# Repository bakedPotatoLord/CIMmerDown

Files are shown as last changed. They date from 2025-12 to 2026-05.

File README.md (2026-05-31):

# CIMmer Down
A project to control 2 drive 2 rev robotics spark ESCs from an arduino nano. 

Coming out of a desire to make use of obsolete parts used by FIRST robotics teams worldwide, we designed a low-cost open source electric longboard. Designed to be accessible to high-school and college students to build, using mostly 3d printed and COTS parts, this project aims to provide an interesting and fun entry into the world of RF electronics, motor control, urethane molding, and more. 

Documentation/Development are not yet complete. Help is always appreciated.

## Features
- Handheld remote
- Status LED
- 2 speed modes
- 16mph top speed
- People of the oposite sex may find you more attractive.
- Disconnection detection and e-stop safety.

## More Details

further, yet incomplete documentation can be found at these pages:

- [Electronics](/Electronics.md)
- [Manufacturing](/Manufacturing.md)

## Selected Media

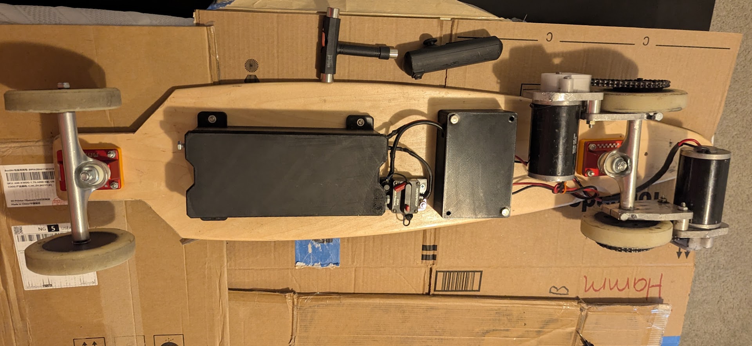
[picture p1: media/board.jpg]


## Why is is called that?
the `CIM` from CIMmer down is a reference to FRC [CIM](https://andymark.com/products/2-5-in-cim-motor) motor.

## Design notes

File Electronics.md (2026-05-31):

# Electronics

These electronics were developed organicaly, and evolved from a wired version of the board.
Along the prototyping process, I switched from an arduino Nano as the longboard controller to an arduino Pro mini 3.3v for both systems.
To be fully honest, this happened because I fried all my arduino nanos, and didn't want to wait for more to ship.

## Schematic

You can download a PDF version of the schematic [here](./media/CimmerDown_schematic.pdf).
when the final revision is complete, I'll put a PNG here.

## Construction

Physically constructing the boards will require some [perfboard](https://en.wikipedia.org/wiki/Perfboard), all the components, and some soldering.

Here is a list of the electrical components to assemble before beginning on making the boards:

### Remote

| Component | Symbol | Quantity | Description |
| --- | --- | --- | --- |
| 10k ohm resistor | R[1-5] | 3 | standard through-hole |
| 100k ohm resistor | R[6-7] | 1 | standard through-hole  |
| 3k3 ohm resistor | R[8] | 1 | standard through-hole |
| status LED | D1 | 1 | standard through-hole; color of your choice! |
| Battery | BT4 | 1 | standard 1S 18650 Li-Ion |
| Arduino Pro Mini  | MOD[1-2] | 1 | 3.3v 8Mhz |
| NRF24L01+ | MOD[3-4] | 1 | standard |
| Analog Joystick | MOD7 | 1 | standard |

### Board

### total
| Component | Symbol | Quantity | Description |
| --- | --- | --- | --- |
| 10k ohm resistor | R[1-5] | 5 | standard through-hole |
| 100k ohm resistor | R[6-7] | 2 | standard through-hole  |
| 3k ohm resistor | R[8] | 1 | standard through-hole |
| 20k ohm resistor | R[9] | 1 | standard through-hole |
| status LED | D1 | 1 | standard through-hole; color of your choice! |
| Battery | BT[1-3] | 3 | CNHL 5.9Ah 3S LiPo |
| Battery | BT4 | 1 | standard 1S 18650 Li-Ion |
| CIM Motor | M[1-2] | 2 | standard |
| Arduino Pro Mini  | MOD[1-2] | 2 | 3.3v 8Mhz |
| NRF24L01+ | MOD[3-4] | 2 | standard |
| REV Robotics Spark ESC | MOD[5-6] | 2 | Obsolete and out of production |
| Analog Joystick | MOD7 | 2 | standard |
| Buck convertor | MOD8 | 1 | 12v to 5v |

Some other consumables include solid core wire, solder, and flux if you prefer.

The perfboard will need to be cut or snapped down to size. The remote requires 23x7 smd holes. The board controller requires __ x __ smd holes.

The following link has an image-based guide showing one way to wire up the boards. it is not difinitively, the only way. if you think you know how to do it better, submit a PR or message me.

[Guide](https://photos.app.goo.gl/4bUh6QA9aAVv1GDRA)

## PCB

A PCB version of the boards might be on the way soon, but I don't know if there's enough interest to warrant it. Lmk if you want one, and what you'd be willing to pay for it.

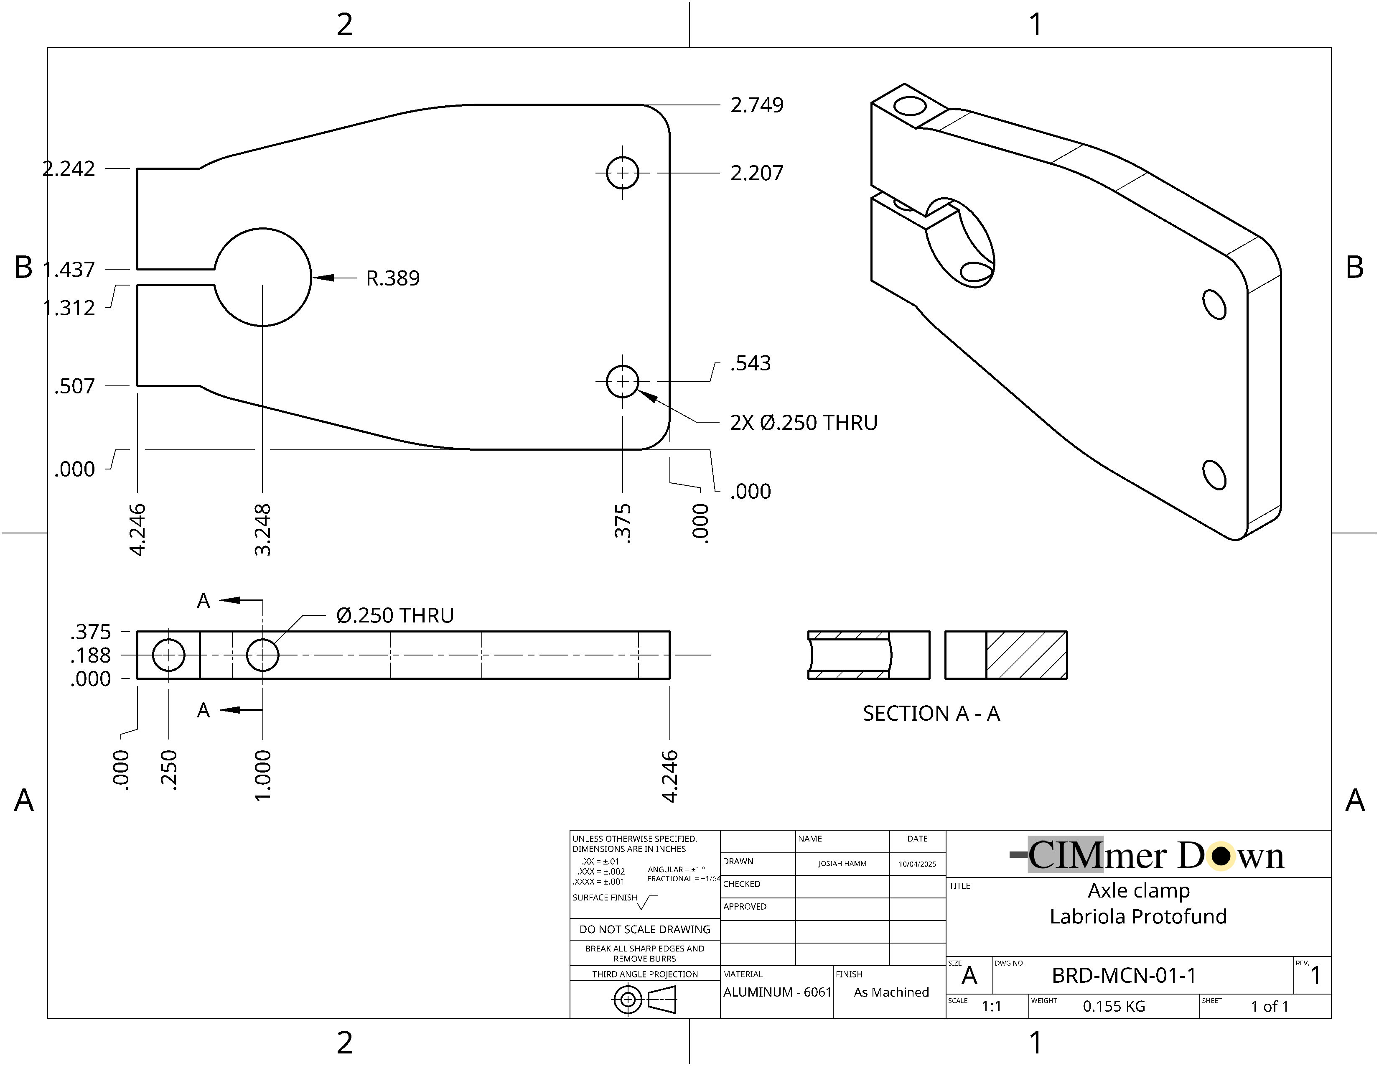
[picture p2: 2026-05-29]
assets/drawings/machining/axle clamp.png

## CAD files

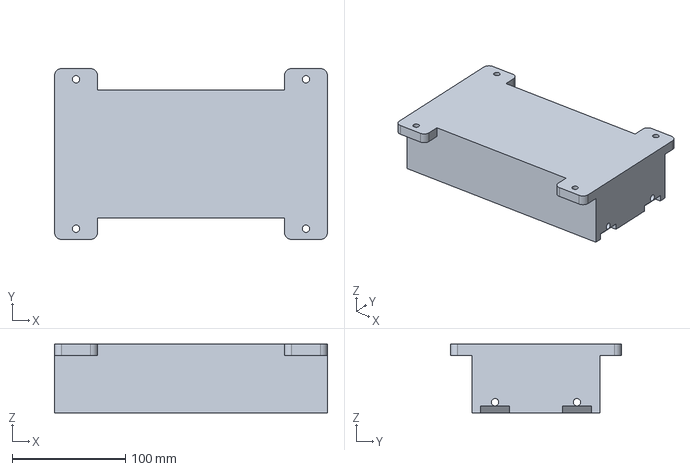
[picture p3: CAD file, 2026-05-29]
assets/STEP/BRD-PRN-03 Battery Box Main.step
241.3 x 151.1 x 61.0 mm

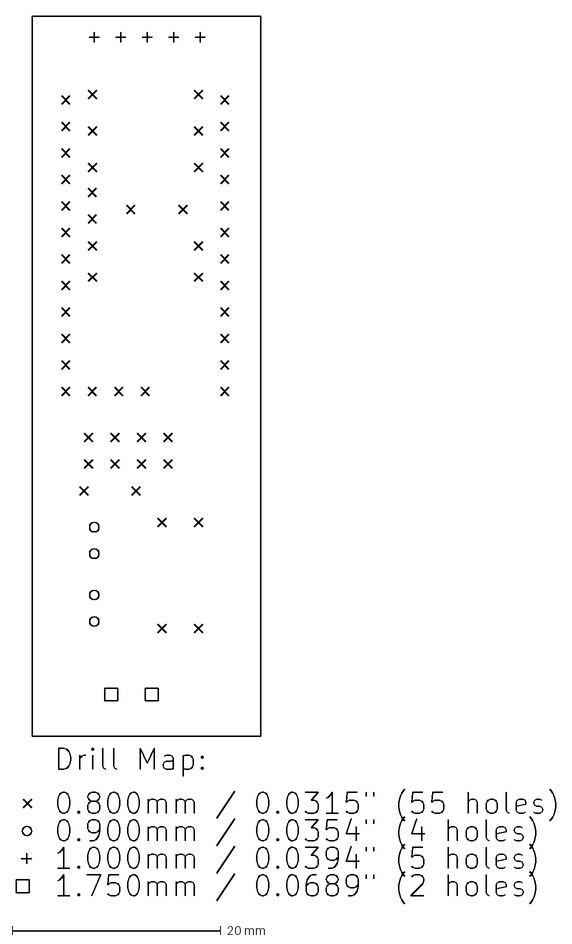
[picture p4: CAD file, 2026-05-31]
assets/circuits/esk8_remote/Esk8_spring_26-PTH-drl_map.dxf
51.7 x 85.0 mm

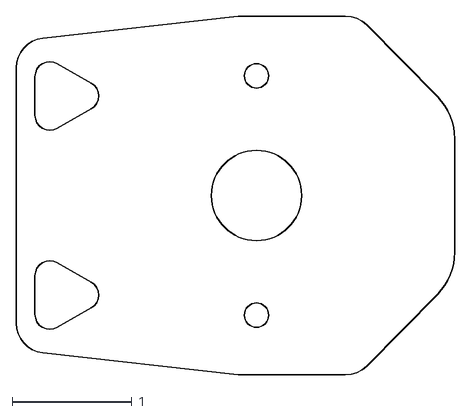
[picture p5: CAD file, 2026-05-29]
assets/drawings/wjet/CIM_mount.dxf
3.66 x 3.00

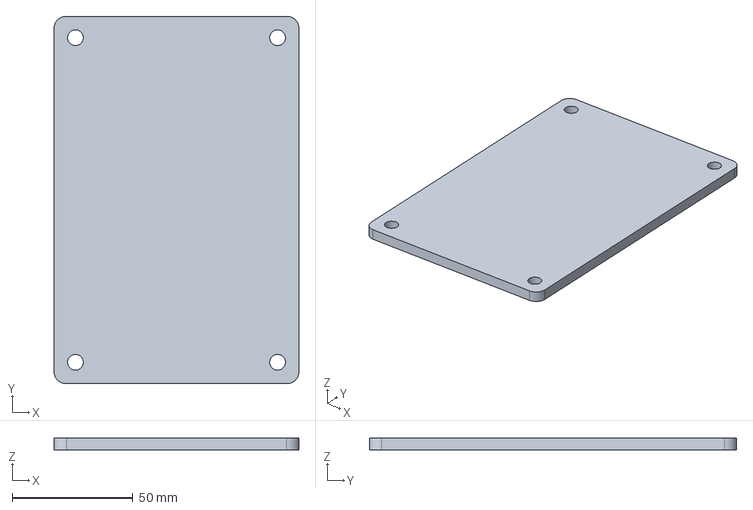
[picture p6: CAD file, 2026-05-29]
assets/STEP/BRD-PRN-02 Electronics Box Lid.step
101.6 x 152.4 x 5.08 mm

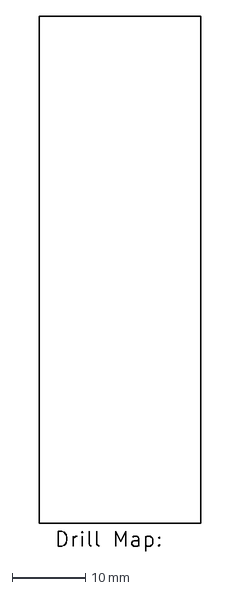
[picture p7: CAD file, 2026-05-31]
assets/circuits/esk8_remote/Esk8_spring_26-NPTH-drl_map.dxf
21.9 x 72.8 mm

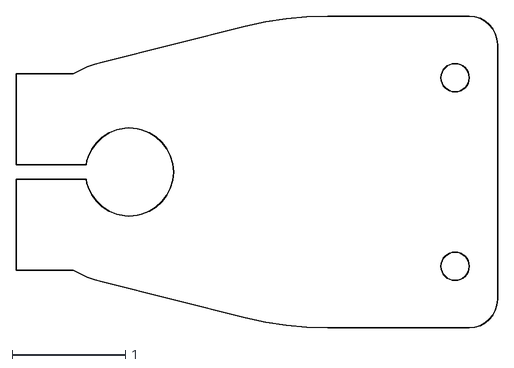
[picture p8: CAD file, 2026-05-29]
assets/drawings/wjet/axle_clamp.dxf
4.25 x 2.75

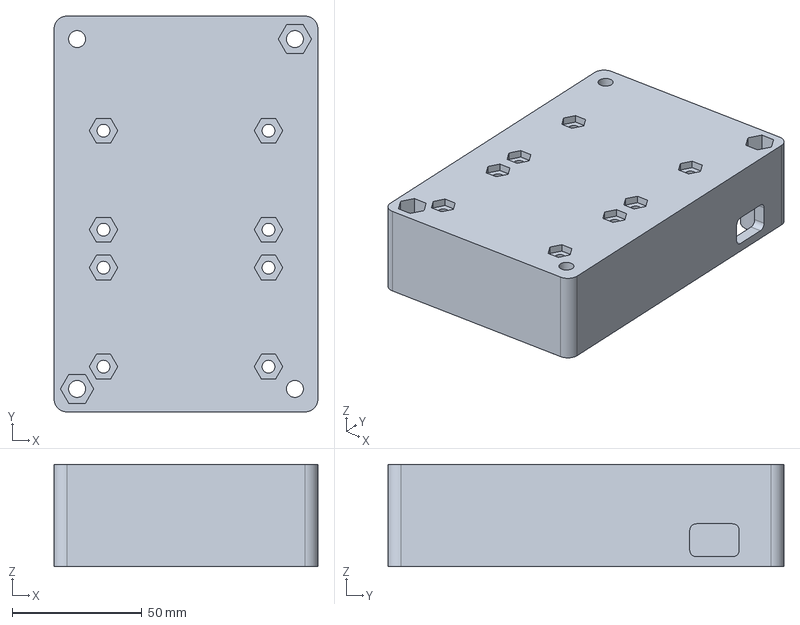
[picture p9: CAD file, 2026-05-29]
assets/STEP/BRD-PRN-01 Electronics Box Housing.step
101.6 x 152.4 x 39.4 mm

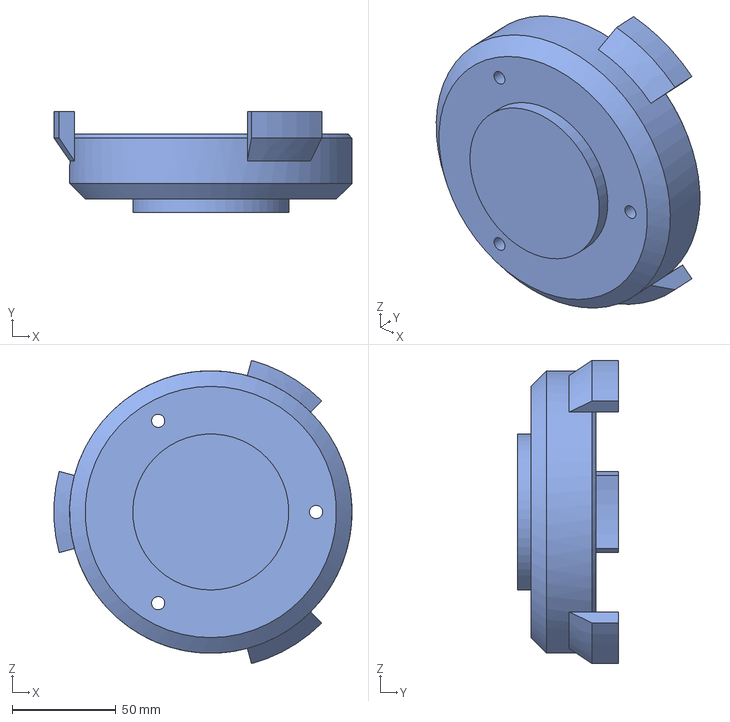
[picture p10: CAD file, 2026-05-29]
assets/STEP/BRD-WHL-05 Mold Bottom.step
143.8 x 48.6 x 146.4 mm

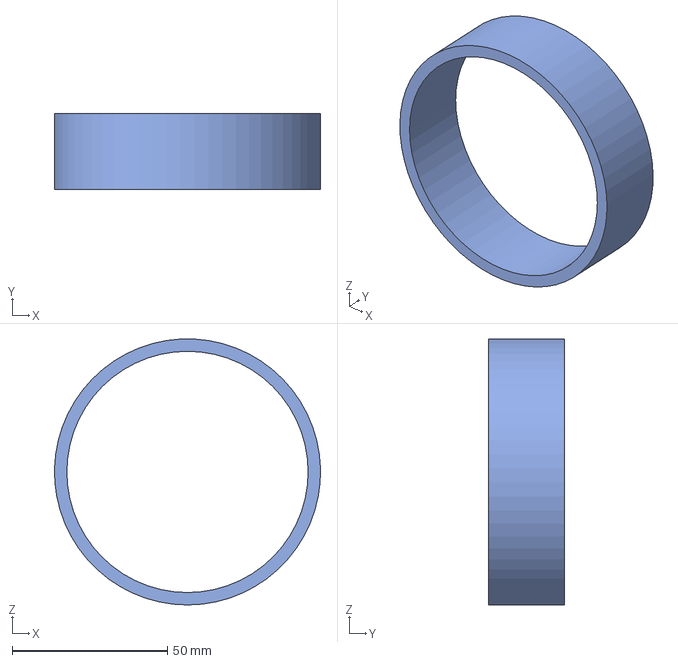
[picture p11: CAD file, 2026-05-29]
assets/STEP/BRD-WHL-03 Modifier Mesh.step
85.6 x 24.4 x 85.5 mm

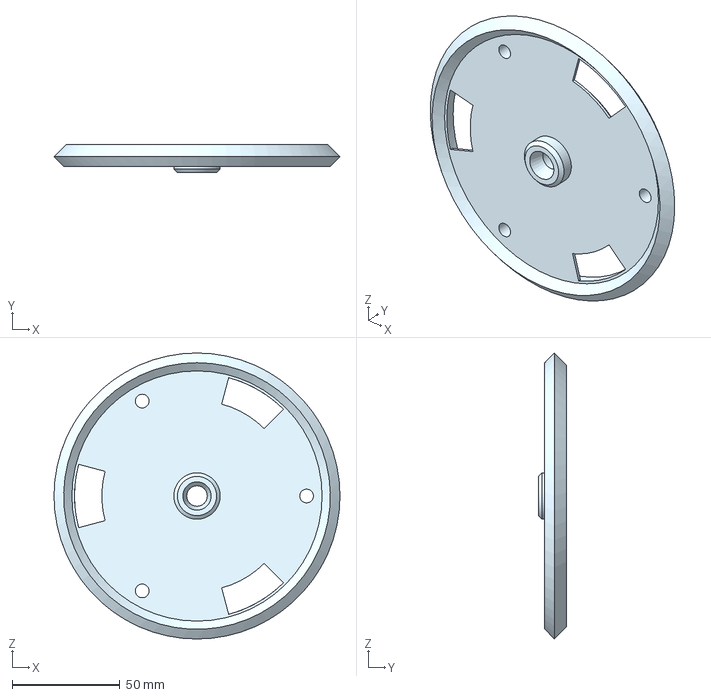
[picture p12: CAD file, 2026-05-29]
assets/STEP/BRD-WHL-06 Mold Top.step
132.6 x 13.1 x 132.6 mm

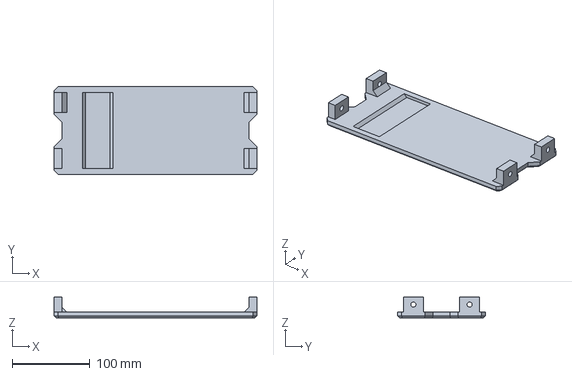
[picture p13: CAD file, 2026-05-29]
assets/STEP/BRD-PRN-04 Battery Box Lid.step
261.6 x 113.0 x 26.7 mm

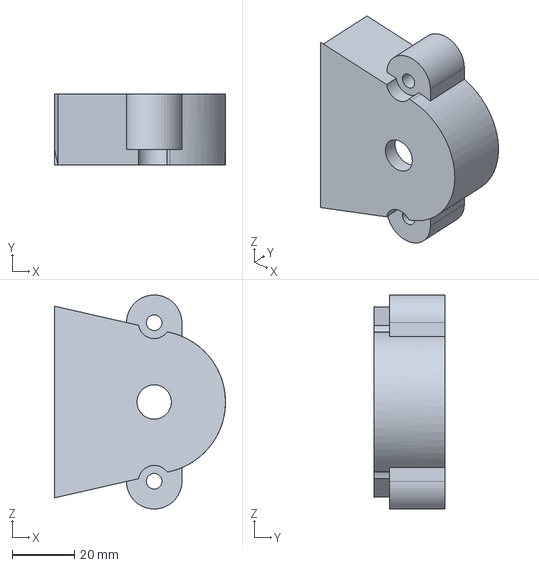
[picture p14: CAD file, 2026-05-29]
assets/STEP/BRD-MCN-05 Sprocket Cover.step
54.8 x 22.9 x 68.6 mm

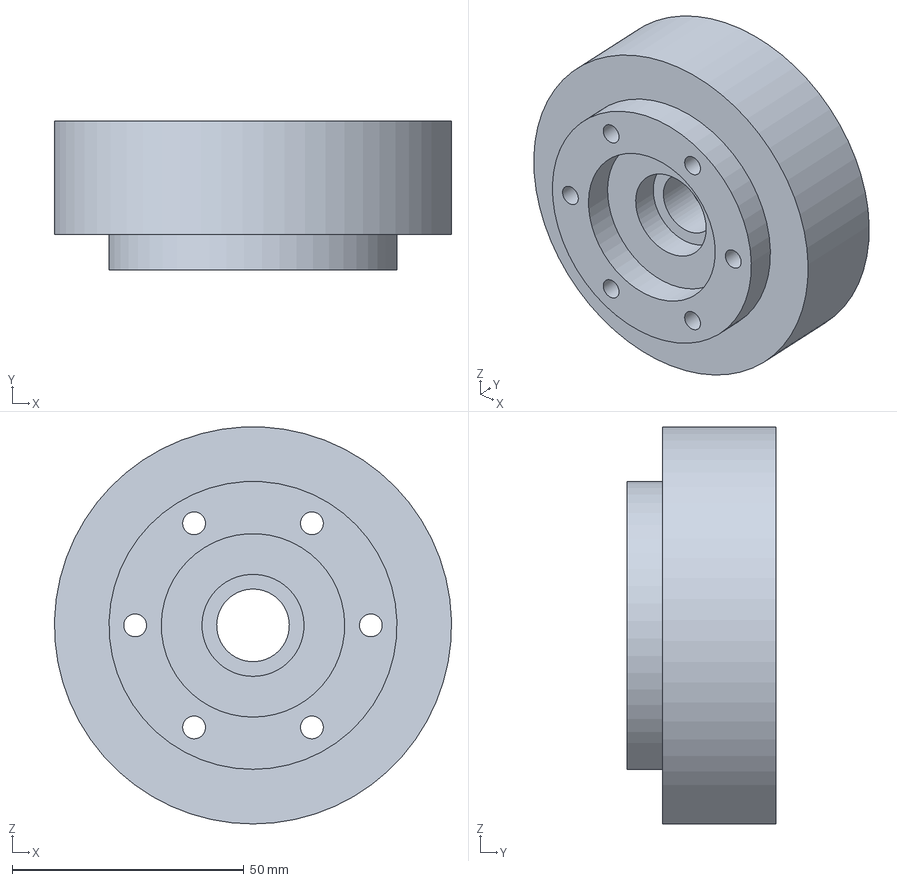
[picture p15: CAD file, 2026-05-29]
assets/STEP/BRD-WHL-01 Powered Hub.step
85.6 x 32.0 x 85.5 mm

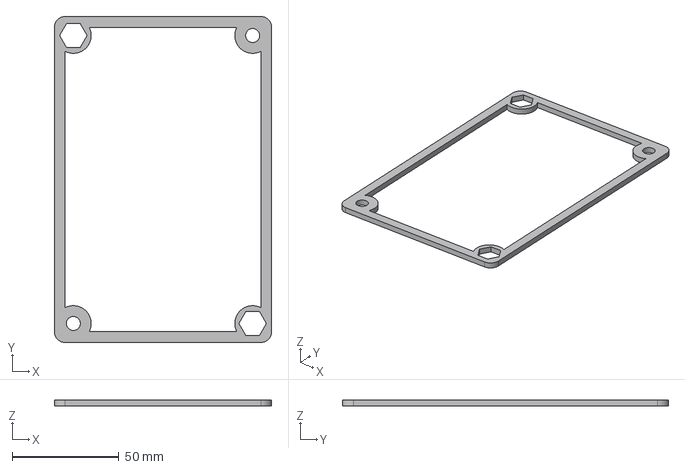
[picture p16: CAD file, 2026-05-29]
assets/STEP/BRD-PRN-05 Gasket.step
101.6 x 152.4 x 3.00 mm

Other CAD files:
assets/STEP/BRD-WHL-04 Unpowered Hub.step
assets/STL/BRD-MCN-05 Sprocket Cover.stl
assets/STL/BRD-PRN-01 Electronics Box Housing.stl
assets/STL/BRD-PRN-02 Electronics Box Lid.stl
assets/STL/BRD-PRN-03 Battery Box Main.stl
assets/STL/BRD-PRN-04 Battery Box Lid.stl
assets/STL/BRD-PRN-05 Gasket.stl
assets/STL/BRD-WHL-01 Powered Hub.stl
assets/STL/BRD-WHL-03 Modifier Mesh.stl
assets/STL/BRD-WHL-04 Unpowered Hub.stl
assets/STL/BRD-WHL-05 Mold Bottom.stl
assets/STL/BRD-WHL-06 Mold Top.stl

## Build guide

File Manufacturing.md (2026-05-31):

# Manufacturing

This is a hastily typed guide on how to build the Cimmer Down longboard. If you are reading this and actually want to make one of these, send me an email, and I'd love to update it for you.

the [CAD](https://cad.onshape.com/documents/5249c8cdbb13477b15d09ab3/w/cd4df9ff8f9b6375afbf69f9/e/7a66caf929776ec3109af745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) is your best friend for this process. It will help you understand what part is what, and how everything fits together.

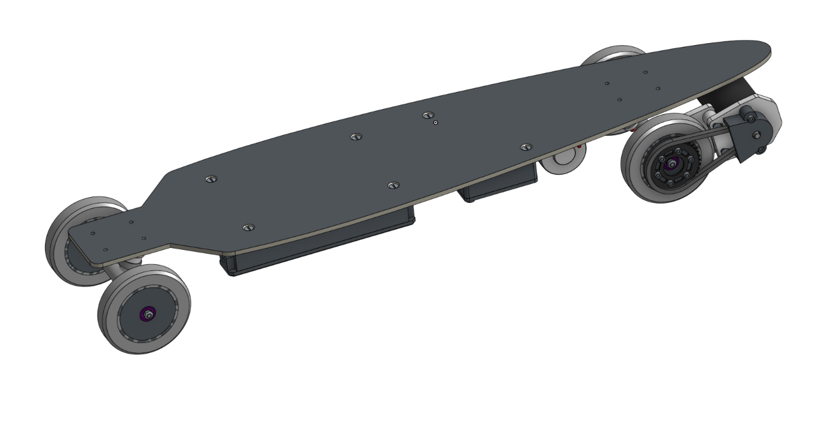
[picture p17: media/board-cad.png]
CAD of the longboard


## BOM

| Item | Quantity | Name | Part number | Description | Material | Mass |
|---|---|---|---|---|---|---|
| 1 | 1 | Longboard Deck | | | Maple, Hard | 0.755 kg |
| 2 | 1 | Electronics Box Lid | BRD-PRN-02  | | 3D Printed PETG | 0.096 kg |
| 3 | 1 | Electronics Box Housing | BRD-PRN-01  | | 3D Printed PETG | 0.202 kg |
| 4 | 2 | SPARK Brushed Motor Controller | REV-11-1200 | SPARK Brushed Motor Controller | - None - | 0.074 kg |
| 5 | 8 | Socket head cap screw #10-32 x 0.625 | | Socket head cap screw #10-32 x 0.625 Stainless Steel | Stainless Steel | 0.004 kg |
| 6 | 8 | Hex machine screw nut #10-32 | | Hex machine screw nut #10-32 Stainless Steel Zinc Plated  | Stainless Steel | 0.002 kg |
| 7 | 4 | Hex machine screw nut 1/4-20 | | Hex machine screw nut 1/4-20 Stainless Steel Zinc Plated  | Stainless Steel | 0.003 kg |
| 8 | 1 | Arduino Nano | | arduino nano | N/A | 0.006 kg |
| 9 | 3 | CNHL 3S Lipo | 520903EC5 | CNHL 3S Lipo | - None - | 0.395 kg |
| 10 | 1 | Battery Box Main | BRD-PRN-03  | | 3D Printed PETG | 0.703 kg |
| 11 | 1 | Battery Box Lid | BRD-PRN-04  | | 3D Printed PETG | 0.276 kg |
| 12 | 6 | Hex nut 1/4-20 | | Hex nut 1/4-20 Stainless Steel | Stainless Steel | 0.004 kg |
| 13 | 2 | Hex cap screw 1/4-20 x 0.75 | | Hex cap screw 1/4-20 x 0.75 Stainless Steel | Stainless Steel | 0.008 kg |
| 14 | 2 | Axle Clamp | BRD-MCN-01  | | Aluminum - 6061 | 0.155 kg |
| 15 | 2 | CIM mount | BRD-MCN-02  | | Aluminum - 6061 | 0.153 kg |
| 16 | 4 | ROUND Spacer 0.75 in | BRD-MCN-03  | | Aluminum - 6061 | 0.013 kg |
| 17 | 2 | Socket head cap screw 1/4-20 x 2 | | Socket head cap screw 1/4-20 x 2 Stainless Steel | Stainless Steel | 0.015 kg |
| 18 | 10 | Hex lock nut 1/4-20 | | Hex lock nut 1/4-20 Stainless Steel | Stainless Steel | 0.003 kg |
| 19 | 2 | 10t Aluminum Sprocket (#25, 8mm CIM/NEO Bore, Double Hub) | am-4772 | 10t Aluminum Sprocket (#25, 8mm CIM/NEO Bore, Double Hub) | Aluminum - 7075 | 0.004 kg |
| 20 | 2 | 60 links #25 chain | BRD-MCN-04  | | Roller Chain | 0.098 kg |
| 21 | 2 | Sprocket Cover | BRD-MCN-05  | | 3D Printed PETG | 0.03 kg  |
| 22 | 4 | Hex cap screw 1/4-20 x 1.75 x 0.75 | | Hex cap screw 1/4-20 x 1.75 x 0.75 Stainless Steel | Stainless Steel | 0.014 kg |
| 23 | 2 | CIM Motor | am-0255 | CIM Motor | - None - | 1.27 kg  |
| 24 | 2 | 36t Aluminum Plate Sprocket (#25, 1.125" Round Bore) | 217-2639 | 36t Aluminum Plate Sprocket (#25, 1.125" Round Bore) | Aluminum - 6061 | 0.022 kg |
| 25 | 4 | Urethane tire | BRD-WHL-02  | | Polyurethane | 0.206 kg |
| 26 | 2 | Powered Hub | BRD-WHL-01  | | 3D Printed PETG | 0.173 kg |
| 27 | 8 | 608 bearing | | 608 bearing | N/A | 0.013 kg |
| 28 | 2 | Unpowered Hub | BRD-WHL-04  | | 3D Printed PETG | 0.164 kg |
| 29 | 12 | Socket head cap screw #10-32 x 1.25 | | Socket head cap screw #10-32 x 1.25 Stainless Steel | Stainless Steel | 0.006 kg |
| 30 | 12 | Hex nut #10-32 | | Hex nut #10-32 Stainless Steel | Stainless Steel | 0.002 kg |
| 31 | 4 | Socket head cap screw #10-32 x 1.75 | | Socket head cap screw #10-32 x 1.75 Stainless Steel | Stainless Steel | 0.008 kg |
| 32 | 2 | Trucks | | 55 Ace clasic trucks | N/A | 0.412 kg |
| 33 | 6 | Countersunk Bolt 1/4-20 x 1 | | Countersunk Bolt 1/4-20 x 1 Stainless Steel | Stainless Steel | 0.007 kg |

## Instructions

There are multiple manufacturing methods used to create this board. I will discuss each and provide the files here. feel free to skip around and make the parts in any order you prefer

### 3D printing

The following parts are 3D printed:  BRD-PRN-02,BRD-PRN-01,BRD-PRN-03,BRD-PRN-04,BRD-MCN-05,BRD-WHL-01

These parts are not part of the final product, but are molds and are requred for urethane molding: BRD-WHL-05,BRD-WHL-06

Finally, this part is used as a modifier mesh when 3D printing: BRD-WHL-03

All of these files can be downloaded from as a zip archive in [STL](/assets/STL.zip) or [STEP](/assets/STEP.zip) format, as well as individualy from this github repo.

All of the parts for the board are recommended to be printed in PETG with at least 4 walls. chances are these parts will take a beating, so the many walls are recommended to protect the things on the inside.

The gasket for the electronics box is recommended to be printed in TPU if available, but the box works fine without it. It will just be slightly less water resistant.

The molds for the wheels can be printed in low-infill PLA, or whatever is cheapest for you. 

The modifier mesh can be used on the exterior of both the powered and Unpowered hub to enhance surface area for the urethane to grip. you can learn more about modifier meshes in this [article](https://blog.prusa3d.com/model-with-prusaslicer-modifier-meshes-tutorial_30438/). It will be slightly different based on your slicer.

### Metal Manufacturing

If you don't want to do this step, reach out to me, and I can get you a quote to manufacture the parts you need. Alternatively, you can send the files to a manufacturing service to get them made. here, I'll attach the part drawings for the machined parts. I found the plates very helpful to waterjet, so I'll include a DXF of the faces of those that you can plug into waterjet software.

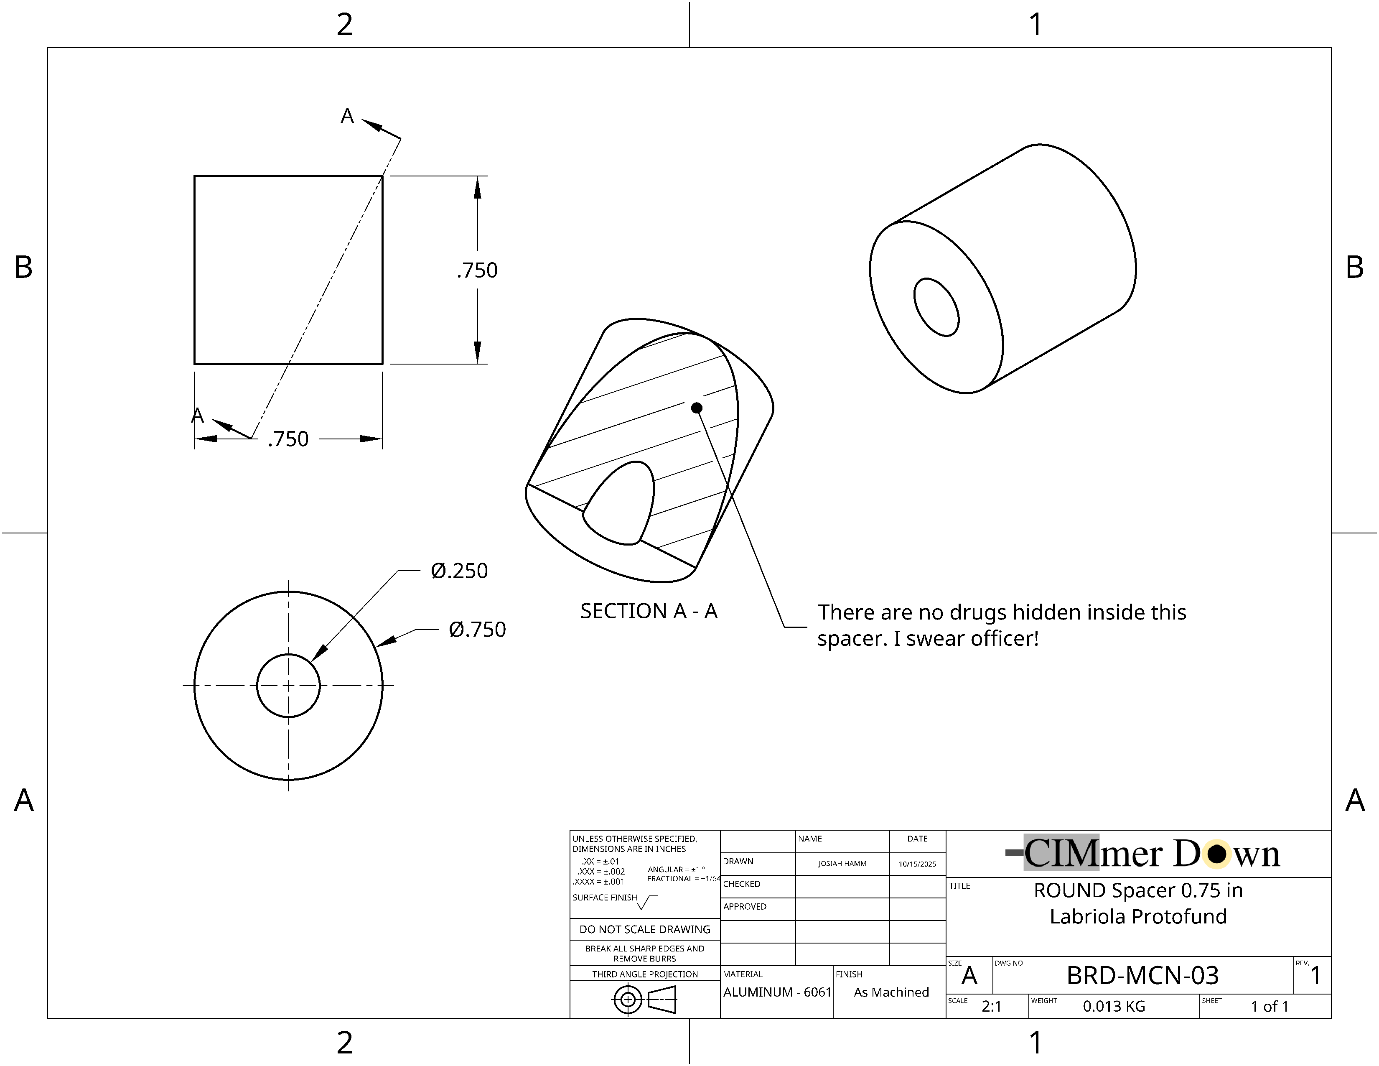
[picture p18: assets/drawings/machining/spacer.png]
spacer drawing

Axle clamp drawing
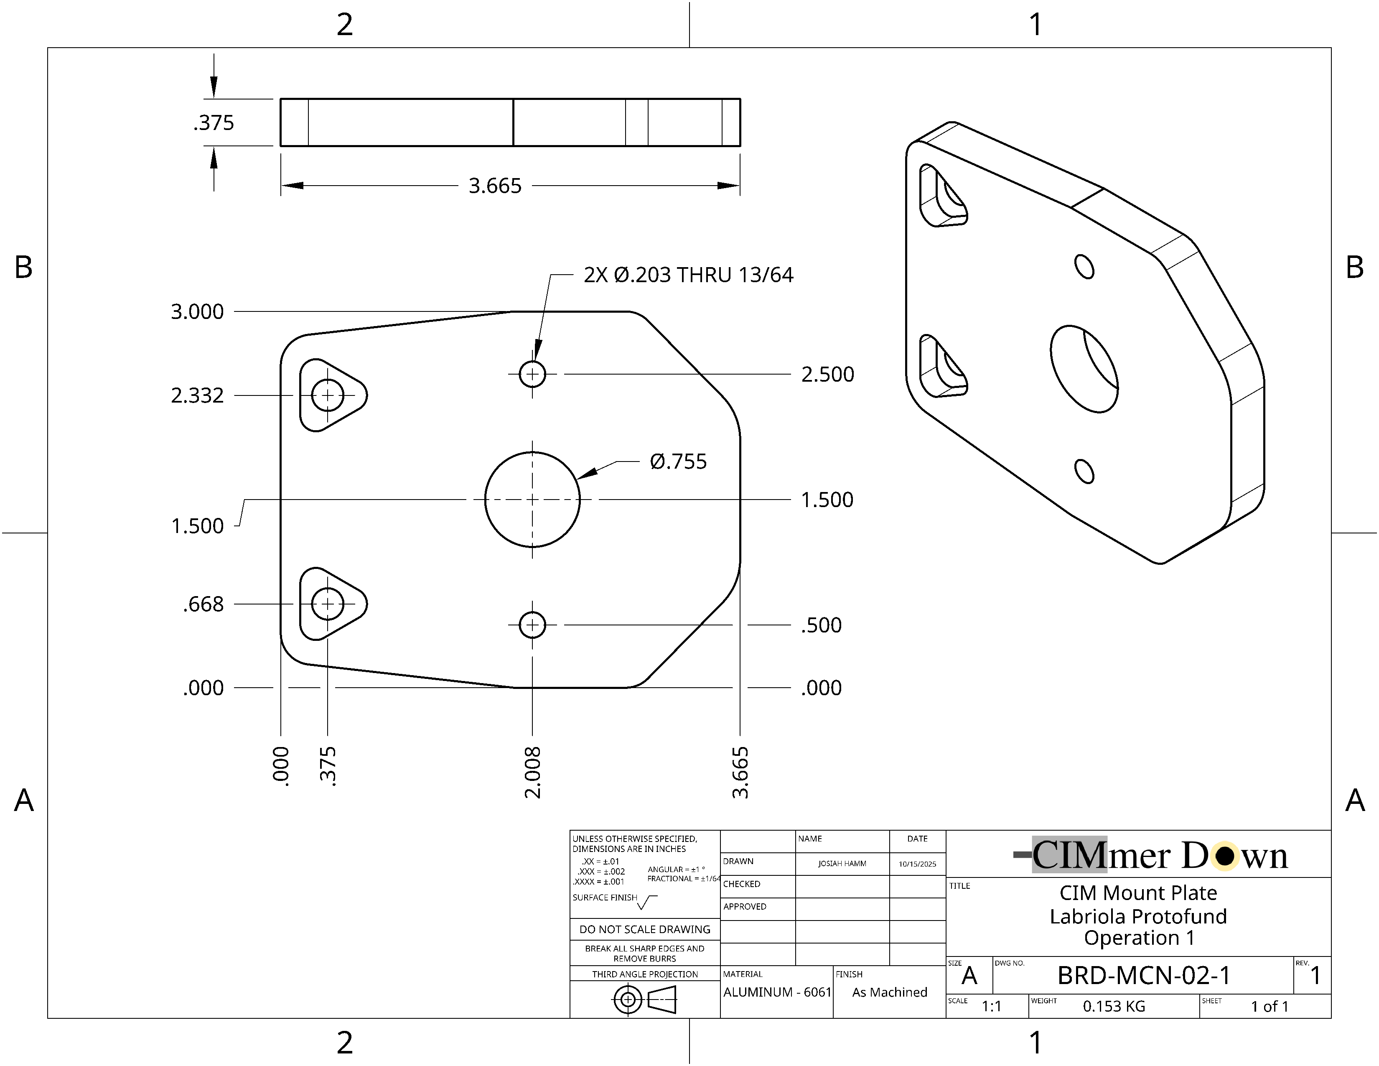
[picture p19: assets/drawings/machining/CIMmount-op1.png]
CIM mount op 1

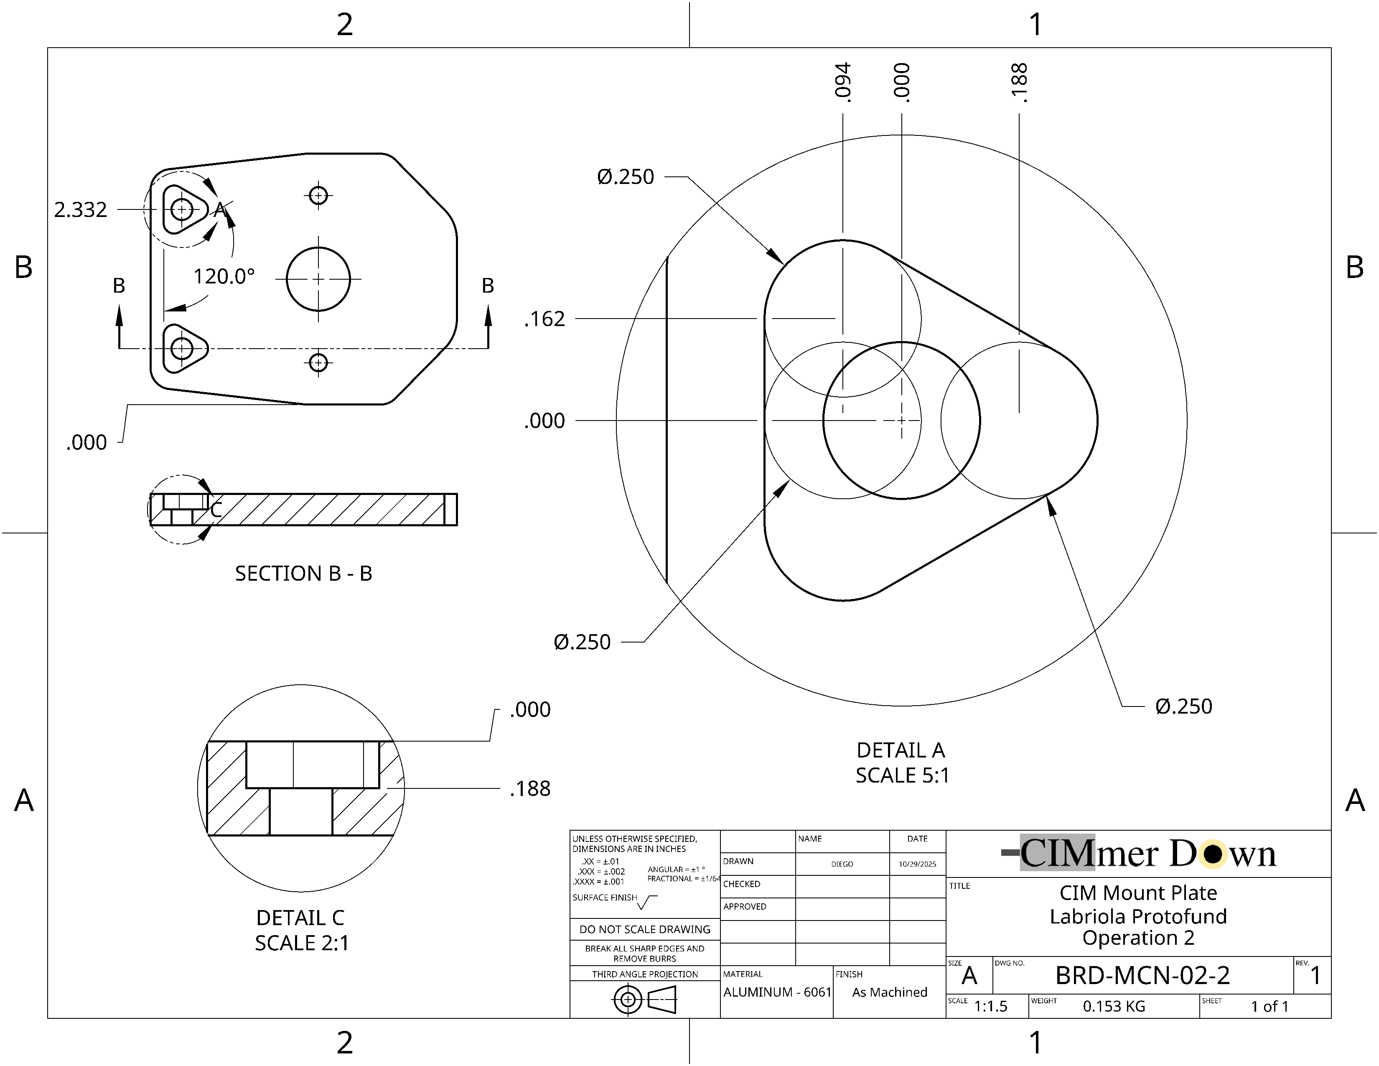
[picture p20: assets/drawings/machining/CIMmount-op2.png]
CIM mount op 2


The DXFs for the sheet-cut parts can be found [here](https://github.com/bakedPotatoLord/CIMmerDown/tree/main/assets/drawings/wjet).

My general order of operations was to waterjet out the profiles of the sheet parts, and then drill them out on the manual mill.
the triangle holes need to be cut on a rotary table, or with a CNC mill. These parts are likely small enough for a Desktop Mill if that's all you have access to. 

The spacers could probably be 3D printed if you don't have a lathe. Just make sure they're printed in PETG with max wall loops.

### Urethane casting

To urethane cast, I used [this resin](https://www.amazon.com/Simple-Resin-Enduro-Flex-Polyurethane/dp/B0B4P9C7T7). This step will require having at least one mold printed, though having 2 will make this process much faster. Here are the steps

- Cover a surface with cardboard or some other protectant
- Fill bottom holes of mold(s) with hot glue, and do not 
- Apply petroleum jelly to entire mold. don't skimp out, or you'll make things much harder for yourself down the line. Make sure all surfaces of the mold get some petroleum jelly on them.
- Calculate how much mass of each part of the urethane you need. the volume of the wheel is 10.486353 in^3, the density is 0.67 oz/in^3, which means that the total mass should be 7.0216 oz, or about 3.511 oz of each part. if you are doing 2 wheels, this can be doubled.
- Pour part a liquid into a tared disposable cup on a scale, get as close to the target volume as possible. pour part b into a tared disposable cup, and get to the same ammount as of part a. if you went over on part a, also go over on part b. 
- Get a stopwatch ready
- As you press start on the stopwatch, pour both parts into a new disposable cup.
- using a popsicle stick, stir the mixture well for 5 minutes, keeping the stick touching the outside of the cup, to minimize bubble creation. the 
- pour the urethane into the molds as quickly as possible wire remaining control of the flow. the mixtuure will be hardening as you pour. use the multiple pout holes if the urethane is not flowing quickly enough. the urethane will become basically unusable after 6-7 minutes.
- let the urethane sit for about 24 hours.
- Pry it out of the mold with a screwdriver, and press it out with the bottom holes until it come loose. This may take a while if you didn't apply the petroleum jelly very liberally

### Woodworking on the Board

I cut the slots into the skate deck using a jigsaw, though a manual saw would work as well. It's recomended to seal the board with wood sealant to keep the boards from delaminating. drilling the holes isn't terribly hard. I sketched out the general placement with a pencil, and then marked the center of the holes with a marker using the 3D printed boxes as a template.

### Media

You can view images for this whole process [here](https://photos.app.goo.gl/PT1SKgsLKWnoJaoL6)

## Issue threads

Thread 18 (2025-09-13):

update electronics for radio board

bakedPotatoLord, 2025-09-13:

bakedPotatoLord, 2025-09-30:
sample code here:

forum.arduino.cc/t/simple-nrf24l01-2-4ghz-transceiver-demo/405123/2

bakedPotatoLord, 2025-09-30:
[Scheme-it-export-skateboard-2025-09-30-09-09.pdf](https://github.com/user-attachments/files/22622453/Scheme-it-export-skateboard-2025-09-30-09-09.pdf)

updated wiring diagram here

bakedPotatoLord, 2025-10-01:
re-updated wiring diagram here:

[Scheme-it-export-skateboard-2025-09-30-16-56.pdf](https://github.com/user-attachments/files/22644770/Scheme-it-export-skateboard-2025-09-30-16-56.pdf)

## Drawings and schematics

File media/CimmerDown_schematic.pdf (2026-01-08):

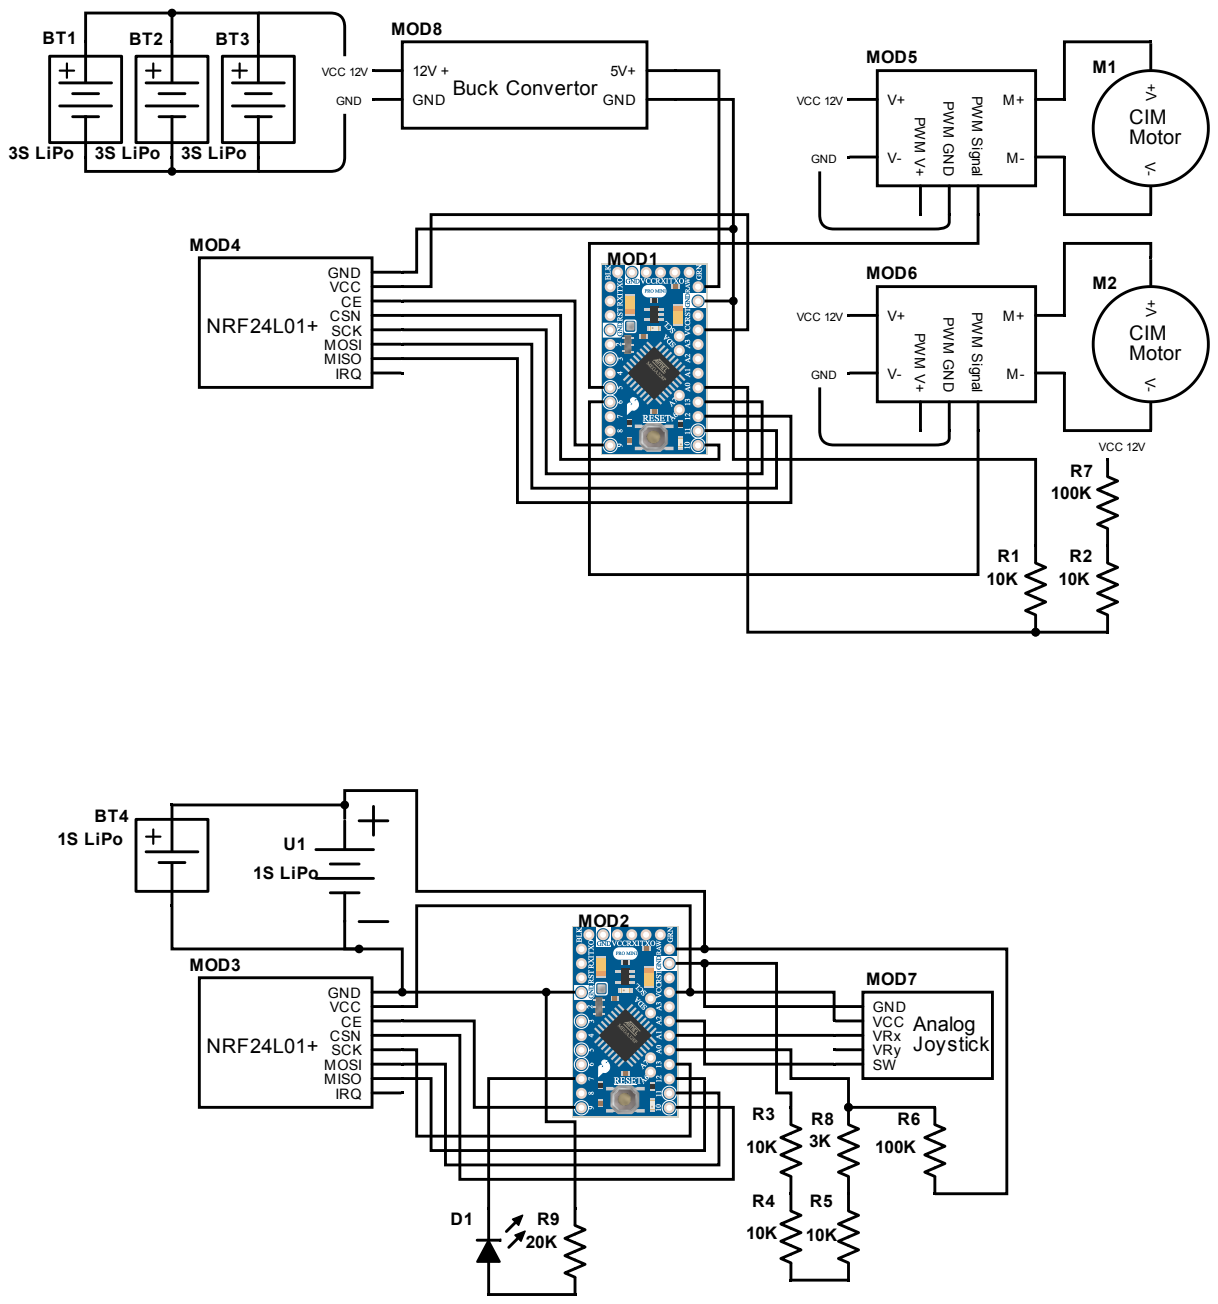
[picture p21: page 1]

TXO RXI RST VCCRXITXO

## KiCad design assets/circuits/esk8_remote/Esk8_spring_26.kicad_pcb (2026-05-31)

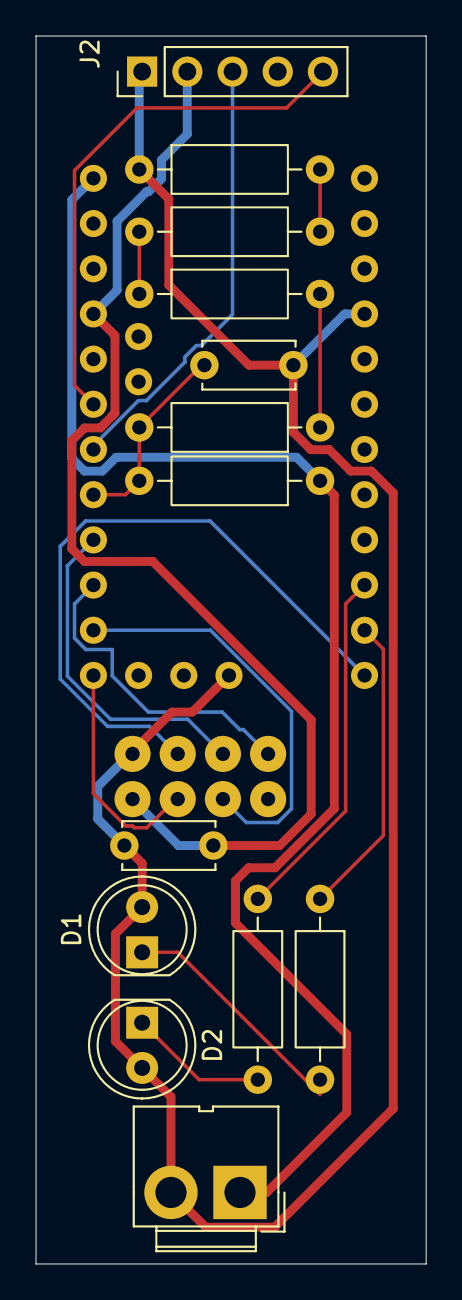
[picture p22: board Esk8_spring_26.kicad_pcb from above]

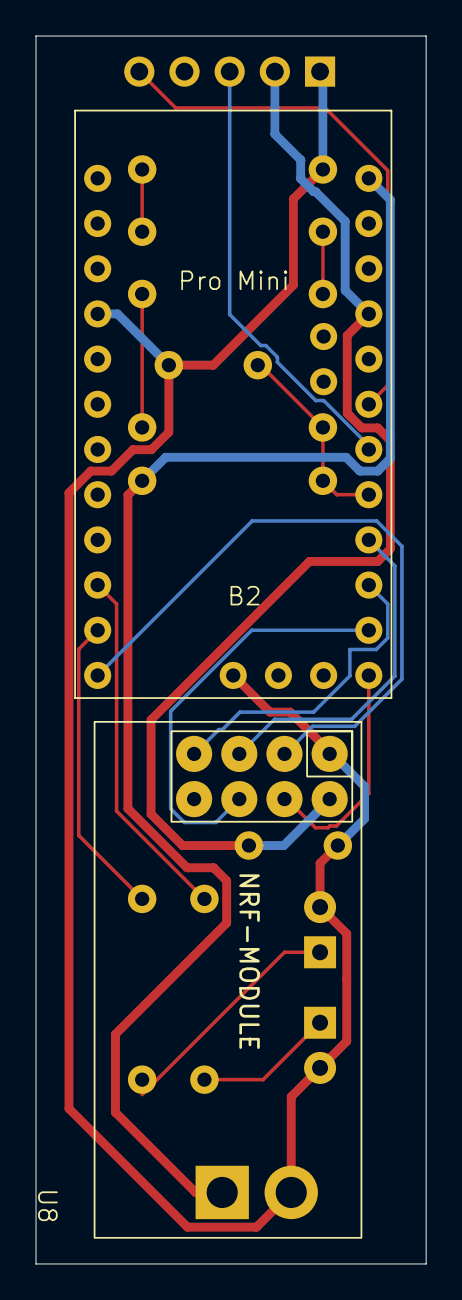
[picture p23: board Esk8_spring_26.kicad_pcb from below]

Board: 2 copper layers, 21.9 x 69.0 mm, 15 parts (2 on the bottom side), 18 nets.

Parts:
B2: ARDUINO_PRO_MINI; ProMini
C1, C2: 100uf; C_Disc_D5.0mm_W2.5mm_P5.00mm
D1, D2: CHIP-FLAT-B_0603-0.35MM; LED_D5.0mm
J1: Conn_01x02_Pin; JWT_A3963_1x02_P3.96mm_Vertical
J2: Conn_01x05_Pin; PinHeader_1x05_P2.54mm_Vertical
R1, R2, R3: 10k; R_Axial_DIN0207_L6.3mm_D2.5mm_P10.16mm_Horizontal
R4: 3.3k; R_Axial_DIN0207_L6.3mm_D2.5mm_P10.16mm_Horizontal
R5: 100k; R_Axial_DIN0207_L6.3mm_D2.5mm_P10.16mm_Horizontal
R6, R7: 220; R_Axial_DIN0207_L6.3mm_D2.5mm_P10.16mm_Horizontal
U8: NRF-MODULE; NRF24Lo1

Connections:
+3.3V: B2.21 (VCC), C1.1, J2.2, U8.2 (VCC)
GND: B2.4 (GND@2), C1.2, C2.2, D1.2 (C), D2.2 (C), J1.2, J2.1, R1.1, U8.1 (GND)
unnamed: B2.10 (7), R6.1
unnamed: B2.11 (8), R7.1
unnamed: B2.15 (12), U8.7 (MISO)
unnamed: B2.16 (13), U8.5 (SCK)
unnamed: B2.12 (*9), U8.3 (CE)
unnamed: B2.13 (*10), U8.4 (CSN)
unnamed: B2.14 (*11), U8.6 (MOSI)
unnamed: B2.17 (A0), C2.1, R4.2, R5.2
unnamed: B2.18 (A1), J2.3
unnamed: B2.19 (A2), J2.5
unnamed: B2.24 (RAW), J1.1, R5.1
unnamed: D1.1 (A), R7.2
unnamed: D2.1 (A), R6.2
unnamed: R1.2, R2.1
unnamed: R2.2, R3.1
unnamed: R3.2, R4.1

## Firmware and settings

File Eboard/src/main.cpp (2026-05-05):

#include "shared.h"

//if REMOTE is not defined, assume board.
#ifdef REMOTE
  #include "controller.h"
#else
  #include "board.h"
#endif

#include "Arduino.h"
#include <avr/sleep.h>


// ==========================================================
// setup() — Runs once on startup
// ==========================================================
void setup() {
  #ifdef _debug
  Serial.begin(115200);
  #endif

  #ifdef REMOTE
    controllerSetup();  // Initialize radio for remote control
  #else
    boardSetup();
  #endif

  #ifdef _debug
  Serial.println("debug");
  #else
  Serial.println("no debug");
  #endif


}

// ==========================================================
// loop() — Main control loop, runs continuously
// ==========================================================

u32 lastLoop = 0;

void loop() {
  u32 now = millis();
  if(now - lastLoop > CYCLE_WAVELEN){ 
    #ifdef _debug
    Serial.print("\nnow: ");
    Serial.println(now);
    #endif
    lastLoop = millis();
    #ifdef REMOTE
      controllerLoop();  // Initialize radio for remote control
    #else
      boardLoop();
    #endif
  }else{
    set_sleep_mode(SLEEP_MODE_IDLE);
    sleep_enable();
    sleep_cpu();
    sleep_disable();
  }
}

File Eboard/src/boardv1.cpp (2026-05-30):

#include <Servo.h>
#include "RF24.h"
#include <Arduino.h>
#include "board.h"
#include "shared.h"

// === Pin Definitions ===
#define ESC1Pin 5        // ESC #1 control signal pin
#define ESC2Pin 6        // ESC #2 control signal pin
#define VDIV_PIN 14 // Voltage divider pin A0

#define VDIV_R1 10e3f // resistor from A0 to GND
#define VDIV_R2 110e3f // resistor from VCC RAW to A0
#define VDIV_REF 1.1f // reference voltage 

#define SOFT_MULTIPLIER 0.918939


// #define RAMP_SECS 2
// #define RAMP_RATE_SLOW  (SPEED_SLOW_FWD - SPEED_STOP) * RAMP_SECS / CYCLE_FREQ
// #define RAMP_RATE_FAST  (SPEED_FAST_FWD - SPEED_STOP) * RAMP_SECS / CYCLE_FREQ

//calibration: real: 12.13, measured, 13.2
// multiplier: 12.13 / 13.2 = 0.919

//convert raw ADC value to input voltage
#define CONVERT_VDIV(raw) (raw * (VDIV_REF / 1023.0f) ) * (VDIV_R1 + VDIV_R2) / VDIV_R1 * SOFT_MULTIPLIER

#define CE_PIN 9
#define CSN_PIN 10

// === Global Objects ===
Servo esc1, esc2;
static RF24 radio(CE_PIN, CSN_PIN);

// === Global State Variables ===
static bool estop = 0;        // Emergency stop flag
static bool foundController = 0;
static bool radioNumber = 1;
const bool role = false;  // true = TX role, false = RX role
static u32 lastMsg;
static u8 batteryState = 0x0;
static u16 lastSpeed = SPEED_STOP;

void boardSetup(){

  // initialize the transceiver on the SPI bus
  if (!radio.begin()) {
    #ifdef _debug
    Serial.println("radio hardware is not responding!!");
    #endif
    while (1) {}  // hold in infinite loop
  }

  Serial.begin(115200);
  esc1.attach(ESC1Pin);
  esc2.attach(ESC2Pin);

  pinMode(VDIV_PIN, INPUT);
  analogReference(INTERNAL);    
  analogRead(VDIV_PIN); //throwaway read
  delayMicroseconds(50);

  while (!Serial) {
    // some boards need to wait to ensure access to serial over USB
  } 
 
  
  radio.setPALevel(RF24_PA_LOW);  // RF24_PA_MAX is default.
  radio.enableDynamicAck();  // ACK payloads are dynamically sized
  radio.setPayloadSize(sizeof(ack_payload_t));
  radio.enableAckPayload();
  radio.setRetries(5, 15);
 
  // set the TX address of the RX node for use on the TX pipe (pipe 0)
  radio.stopListening(addresses[radioNumber]);  // put radio in TX mode
 
  // set the RX address of the TX node into a RX pipe
  radio.openReadingPipe(1, addresses[!radioNumber]);  // using pipe 1
 
  // additional setup specific to the node's RX role
  if (!role) {
    radio.startListening();  // put radio in RX mode
  }


}

void boardLoop(){
  // === Handle Emergency Stop ===
  if (estop) {
    esc1.writeMicroseconds(SPEED_STOP);
    esc2.writeMicroseconds(SPEED_STOP);

    #ifdef _debug
    Serial.println("Emergency Stop!");
    #endif

    return;  // Skip rest of loop
  }

  float battVoltage = CONVERT_VDIV(analogRead(VDIV_PIN));

  packet_t payload;
  ack_payload_t ackPayload = {};

  uint8_t pipe;
  if (radio.available(&pipe)) { // is there a payload? get the pipe number that received it
    foundController = 1;
    uint8_t bytes = radio.getDynamicPayloadSize();  // get the size of the payload
    radio.read(&payload, bytes); // fetch payload from FIFO
    lastMsg = millis();

    u16 speed = payload.throttle;
    
    if(battVoltage < 9.0f){
      batteryState = FLAG_BOARD_BATT_DEAD;
    }
    else if (battVoltage < 9.6f){
      batteryState = FLAG_BOARD_BATT_LOW;
    }else{
      batteryState = 0x0;
    }
    #ifdef _debug
    Serial.print("Board recieved Packet.Sequence number: ");
    Serial.println(payload.seq);
    Serial.print("timestamp:");
    Serial.println(lastMsg);
    Serial.print("Batt Voltage: "); 
    Serial.println(battVoltage);
    Serial.print("Battery flags: "); 
    Serial.println(batteryState);
    Serial.print("Speed: ");
    Serial.println(speed);
    Serial.println();
    #endif

    ackPayload.flags = batteryState;
    radio.writeAckPayload(1, &ackPayload, sizeof(ackPayload));
    if(batteryState != FLAG_BOARD_BATT_DEAD){

      // u16 rampRate = RAMP_RATE_SLOW;
      // if(speed > lastSpeed && speed > SPEED_STOP){ //if accelerating forward
      //   speed = (speed - lastSpeed > rampRate)? lastSpeed + rampRate : speed;
      // }else if(speed <= lastSpeed && speed < SPEED_STOP){
      //   speed = (lastSpeed - speed >  rampRate)? lastSpeed - rampRate : speed;
      // }
      // lastSpeed = speed;
      u16 invertedSpeed = map(speed, 1000,2000,2000,1000);
      esc1.writeMicroseconds(speed);
      esc2.writeMicroseconds(speed);
    }
  }else{
    //no packet available

    u32 m = millis();
    if(foundController && (m - lastMsg > 3000)){
      //if had controller, and no message for 3 seconds
      #ifdef _debug
      Serial.println("Controller lost");
      Serial.println(m);
      Serial.println(lastMsg);
      #endif
      estop = 1;
    }else{
      #ifdef _debug
      Serial.println("waiting for controller");
      Serial.print("batt voltage: ");
      Serial.println(battVoltage);
      #endif
    }
  }
}

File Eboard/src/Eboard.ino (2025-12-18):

#include "board.h"
#include "rf.h"
#include "Arduino_BuiltIn.h"

#define remote


// ==========================================================
// setup() — Runs once on startup
// ==========================================================
void setup() {
  Serial.begin(115200);

  #ifdef remote
    rfSetup();  // Initialize radio for remote control
  #else
    boardSetup();
  #endif
}

// ==========================================================
// loop() — Main control loop, runs continuously
// ==========================================================
void loop() {
  #ifdef remote
    rfSetup();  // Initialize radio for remote control
  #else
    boardLoop();
  #endif
}

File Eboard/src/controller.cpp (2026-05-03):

#include <SPI.h>
#include "RF24.h"
#include "controller.h"
#include "shared.h"
#include <avr/sleep.h>

#define CE_PIN 9
#define CSN_PIN 10


#define SWITCH_PIN (A2+0U)   //16 Mode switch input pin (A2)
#define JOYSTICK_PIN (A1+0U) //15   // Joystick analog input (A1)  
#define LED_PIN_BLUE 7
#define LED_PIN_RED 8
#define DEADBAND 5       // Deadband around neutral (±5 µs out of 1000 µs range)

#define BATT_LOW 3.4f
#define BATT_DEAD 3.2f

#define VDIV_PIN 14 // Voltage divider pin A0

#define VDIV_R1 35e3f // resistor from A0 to GND 
#define VDIV_R2 100e3f // resistor from VCC RAW to A0 
#define VDIV_REF 3.3f // reference voltage 
//convert raw ADC value to input voltage
#define CONVERT_VDIV(raw) (raw * (VDIV_REF / 1023.0f) ) * (VDIV_R1 + VDIV_R2) / VDIV_R1

static RF24 radio(CE_PIN, CSN_PIN);

static bool radioNumber = 0;
bool role = true;  // true = TX role, false = RX role

u16 packetNum = 0;  


Speedmode mode = Speedmode::SLOW; // Start in demo mode
long timestamp; // Last time switch was pressed
bool lastSwitch = 1; // Previous switch state
Status status = Status::await_connect;
u32 lastmsgRecv = 0;

void controllerSetup(){
  pinMode(SWITCH_PIN, INPUT_PULLUP);  // Switch is active LOW
  pinMode(JOYSTICK_PIN, INPUT);
  pinMode(VDIV_PIN, INPUT);
  pinMode(LED_PIN_BLUE, OUTPUT);

  if (!radio.begin()) {
    #ifdef _debug 
    Serial.println(F("radio hardware is not responding!!"));
    while(1){};
    #endif
    status = Status::hardwareFault;
    return;
  }

  //set 2 byte CRCs, and 5 byte address
  radio.setCRCLength(RF24_CRC_16);
  radio.setAddressWidth(ADDR_LEN); 
 
  // Set the PA Level low to try preventing power supply related problems
  // because these examples are likely run with nodes in close proximity to
  // each other.
  radio.setPALevel(RF24_PA_LOW);  // RF24_PA_MAX is default.
 
  radio.enableDynamicAck();  // ACK payloads are dynamically sized
  radio.setPayloadSize(sizeof(packet_t));

  // Acknowledgement packets have no payloads by default. We need to enable
  // this feature for all nodes (TX & RX) to use ACK payloads.
  radio.enableAckPayload();
  radio.setRetries(5, 15);
 
 
  // set the TX address of the RX node for use on the TX pipe (pipe 0)
  radio.stopListening(addresses[radioNumber]);  // put radio in TX mode
 
  // set the RX address of the TX node into a RX pipe
  radio.openReadingPipe(1, addresses[!radioNumber]);  // using pipe 1
 
  // additional setup specific to the node's RX role
  if (!role) {
    radio.startListening();  // put radio in RX mode
  }
}

void controllerLoop(){
  SetLED();

  if(status == Status::hardwareFault){
    return;
  }else if (status == ctrl_batt_dead){
    //disable peripherals
    radio.powerDown();
    // put controller into sleep mode
    set_sleep_mode(SLEEP_MODE_PWR_DOWN);
    sleep_enable();
    sleep_mode();
  }

  struct packet_t payload = {};
  payload.seq = packetNum++;
  payload.flags = FLAG_NONE;

  // === Read Inputs ===
  u16 joystick = analogRead(JOYSTICK_PIN);
  float battery = CONVERT_VDIV( (float) analogRead(VDIV_PIN));
  unsigned char switchVal = !digitalRead(SWITCH_PIN);  // Active when pressed

  if(battery <= BATT_LOW) status = Status::ctrl_batt_low;
  if(battery <= BATT_DEAD){
    status = Status::ctrl_batt_dead;
    return;
  } 

  #ifdef _debug
  Serial.print("Joystick: ");
  Serial.print(joystick);
  Serial.print(", Switch: ");
  Serial.println(switchVal);
  Serial.print("Battery: ");
  Serial.println(battery);
  #endif

  // Detect rising edge (button pressed now, not pressed before)
  if (!lastSwitch && switchVal) {
    timestamp = millis();
  }

  // If switch is currently held down...
  if (switchVal) {
    // Held for >1.5 seconds → toggle mode
    if (millis() - timestamp > 1500) {
      mode = (Speedmode) !mode;
      timestamp = millis();

      //trigger mode switch
      payload.flags = (mode == FAST) ? FLAG_FAST : FLAG_SLOW;
    }
  }

  // Update last switch state
  lastSwitch = switchVal;

  //map joystick val to pwm out
  int PWMOut = (mode == FAST)
    ? map(joystick, 0, 1023, SPEED_FAST_REV, SPEED_FAST_FWD)
    : map(joystick, 0, 1023, SPEED_SLOW_REV, SPEED_SLOW_FWD);

  // Apply deadband around stopSpeed
  if (abs(PWMOut - SPEED_STOP) < DEADBAND) {
    PWMOut = SPEED_STOP;
  }
  payload.throttle = PWMOut;

  unsigned long start_timer = micros();                // start the timer
  bool report = radio.write(&payload, (u8) sizeof(packet_t));  // transmit & save the report
  unsigned long end_timer = micros();                  // end the timer

  if (report) {
    #ifdef _debug
    Serial.println("Transmission successful! ");  // payload was delivered
    Serial.print("Time to transmit = ");
    Serial.print(end_timer - start_timer);
    Serial.print(" us, seq=");
    Serial.println(payload.seq);
    Serial.print(", throttle = ");
    Serial.print(payload.throttle);
    Serial.print(", flags = ");
    Serial.println(payload.flags);
    #endif

    u8 pipe;
    if (radio.available(&pipe)) {  // is there an ACK payload? grab the pipe number that received it
      ack_payload_t received;
      radio.read(&received, sizeof(received));  // get incoming ACK payload
        #ifdef _debug        
        Serial.print("Received ACK packet, battery = ");
        Serial.println(received.flags);
        Serial.println();
        #endif
        status = Status::ok;
        lastmsgRecv = millis();
        if(received.flags & FLAG_BOARD_BATT_LOW){
          status = Status::board_batt_low;
        }else if(received.flags & FLAG_BOARD_BATT_DEAD){
          status = Status::board_batt_dead;
        }
    } else {
      #ifdef _debug
      Serial.println(" no incoming ACK packet\n");  // empty ACK packet received
      #endif
    }

  } else {
    #ifdef _debug
    Serial.println("Transmission failed or timed out");  // payload was not delivered
    #endif
    if(lastmsgRecv != 0 &&
       millis() - lastmsgRecv > 2000 &&
       ( status == ok)){
      //if no ack received in 2 seconds, go back to await connect
      status = Status::await_connect;
      
    }
  }
}
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

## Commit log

2025-08-27 Current Code V1.1
2025-09-01 finalize encoder code
2025-12-18 switch to pio best practices
2025-12-19 wheels spinning
2025-12-25 switch configs to both pro minis
2025-12-27 reconfigure for voltage divider and transistor buzzer
2025-12-27 add more debug prints
2026-01-06 read battery
2026-01-06 add speed debug print
2026-01-07 first pass at status LED
2026-01-07 switch const names
2026-03-15 add vescUart and get connected
2026-03-15 switch to PWM because the VESC is a liar
2026-03-27 add led 2 pin define
2026-04-09 switch to arduino nano for board
2026-04-09 get blue and red LEDs working
2026-04-29 switch to correct arduino board
2026-05-03 combine both boards in one branch
2026-05-29 add 3d printing files
    [BRD-MCN-05 Sprocket Cover.step, BRD-MCN-05 Sprocket Cover.stl, BRD-PRN-01 Electronics Box Housing.step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]
2026-05-29 move assets to assets folder
    [BRD-MCN-05 Sprocket Cover.step, BRD-MCN-05 Sprocket Cover.stl, BRD-PRN-01 Electronics Box Housing.step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]
2026-05-29 complete first two sections of manufacturing
    [CIM_mount.dxf, axle_clamp.dxf]
2026-05-30 revert ramp rate code. needs encoder to work properly.
    [boardv1.cpp]
2026-05-31 add kicad circuit
    [Esk8_spring_26-NPTH-drl_map.dxf, Esk8_spring_26-PTH-drl_map.dxf, Esk8_spring_26.kicad_pcb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]
